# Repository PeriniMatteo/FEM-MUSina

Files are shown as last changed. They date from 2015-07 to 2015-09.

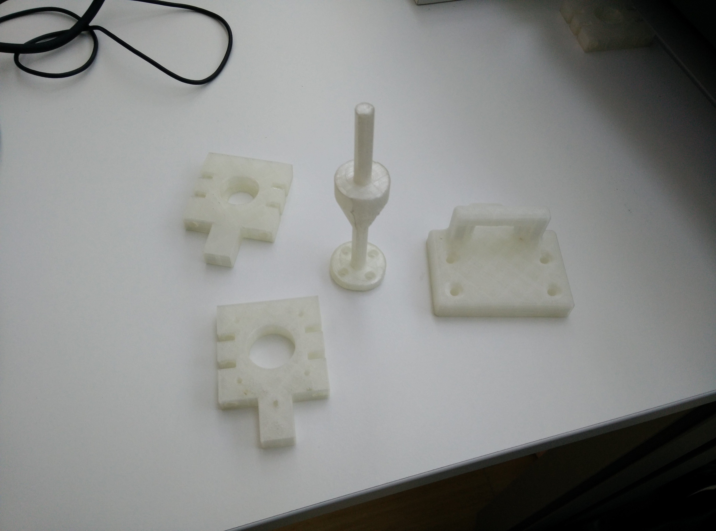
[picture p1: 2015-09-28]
pictures/3D-printed-components.jpg

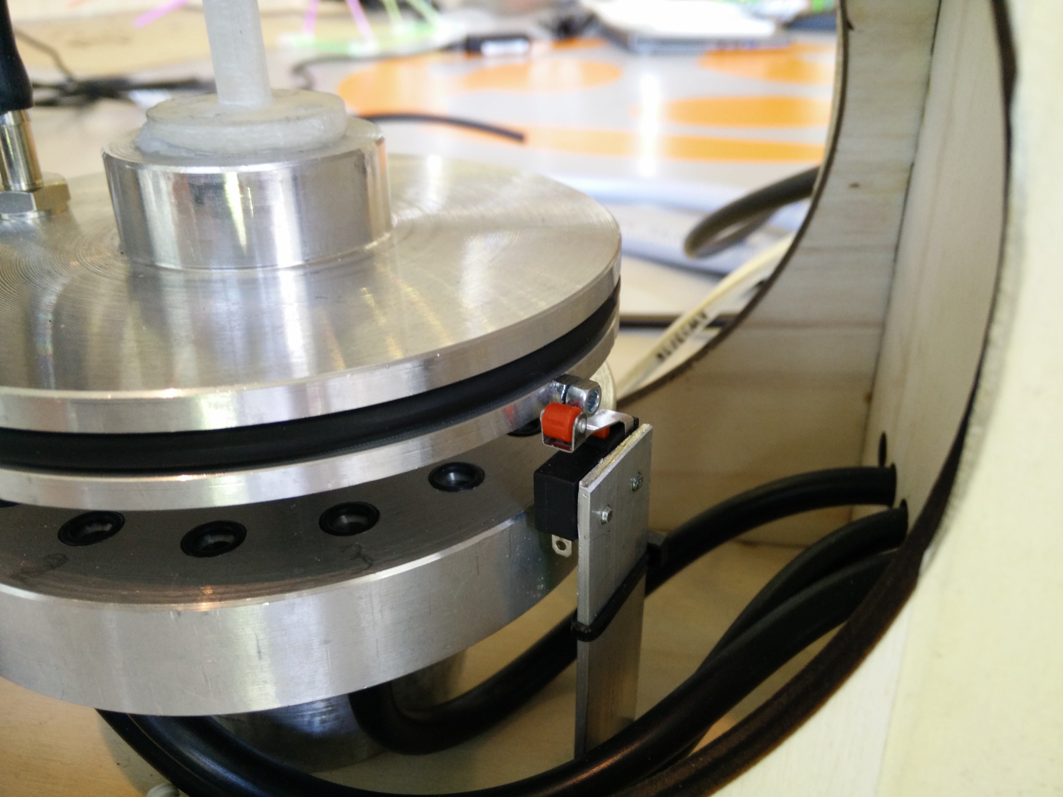
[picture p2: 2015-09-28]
pictures/end-stop-detail.jpg

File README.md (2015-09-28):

# FEM-MUSina
Repository che contiene informazioni sui componenti e strumentazione
necessari per costruire, programmare e gestire l'irrigatore FEM-MUSina.

L'intero progetto riportato è soggetto alla licenza GPL V3 (vedi file
[LICENSE](https://github.com/musefablab/FEM-MUSina/blob/master/LICENSE)).

G.Berti, D.Caset, S.Corradini, T.Dallapè, N.Oradini, M.Perini, G.Toller

FEM-MUSina: a seguito di un'idea partita all'interno della 
[Fondazione Edmund Mach](http://www.fmach.it), il 
[MUSE FabLab](http://fablab.muse.it), laboratorio di fabbricazione
digitale del Museo delle Scienze di Trento, ha contribuito a realizzare
un prototipo di macchina per l'irrigazione domestica di piante in vaso.
Questo progetto è nato con lo scopo di riuscire ad annaffiare svariate
piante solo quando queste ne hanno bisogno. Per fare questo ogni vaso è
dotato di un sensore dell’umidità del suolo e di una propria linea
irrigua. Il sistema, governato da un hardware e da un software creati a
partire dalla piattaforma informatica Arduino, dosa l’acqua in modo
adeguato alle esigenze di ogni pianta. Molti pezzi speciali del
prototipo, ad esclusione di quelli che richiedevano tornitura, sono
stati realizzati con gli strumenti in dotazione al FabLab: taglio laser,
stampante 3D, fresatrice. Nella progettazione si è puntato ad abbassare
i costi riducendo al massimo il numero di elettrovalvole/pompe. Nella
versione attuale, basata su un distributore rotante, una sola
elettrovalvola/pompa può alimentare sedici linee, ma è previsto di
espanderne il numero. Il controller scansiona periodicamente i sensori
di umidità nei vasi e, in base alla risposta, dosa la quantità d’acqua
somministrata a ciascuna pianta.

Gli elementi previsti per la costruzione completa della macchina
comprendono:

- [scheda Arduino](https://store.arduino.cc/product/A000066)
- [shield (autocostruito)](https://github.com/musefablab/FEM-MUSina/tree/master/schematics/pcb)
- [motor shield Arduino](https://www.arduino.cc/en/Main/ArduinoMotorShieldR3)
- componenti elettronici necessari per il circuito Arduino documentati
nella cartella [DATASHEET](https://github.com/musefablab/FEM-MUSina/tree/master/datasheet)
- switch di fine corsa
- servo
- motorino passo passo (Nema 17) 200 passi/giro
- elettrovalvola / pompa (12V)
- cablaggio per i sensori d'umidità
- tubi per flusso acqua
- alimentatore 12V collegato a presa di corrente

I dati e le tavole dei componenti sono reperibili nelle varie
cartelle:

- visualizzazione del modello solido della macchina dalle varie
prospettive - [IMAGES](https://github.com/musefablab/FEM-MUSina/tree/master/images)
- disegni tecnici dei componenti in compensato spesso 8mm da tagliare ed
assemblare ad incastro per il supporto esterno della macchina - 
[LASER](https://github.com/musefablab/FEM-MUSina/tree/master/laser)
- modelli 3D dei componenti di supporto fabbricati con stampa 3D - 
[STL](https://github.com/musefablab/FEM-MUSina/tree/master/stl)
- disegni tecnici delle parti meccaniche in alluminio e in gomma (parte
inferiore e superiore del disco forato, base di supporto al disco,
supporto rotazionale per giunto elastico, cuscinetto, cinghia, sezione
frontale della macchina) - [DRAWING](https://github.com/musefablab/FEM-MUSina/tree/master/drawings)
- schemi dei collegamenti elettronici, breadboard, PCB Arduino - 
[SCHEMATICS](https://github.com/musefablab/FEM-MUSina/tree/master/schematics)
- codice di programmazione dell'Arduino - [SRC](https://github.com/musefablab/FEM-MUSina/tree/master/src/FEM-MUSina)

Assemblare le parti meccaniche tornite e stampate inserendo il tutto nel
case dell'irrigatore completo dei supporti e dei componenti di fissaggio
come mostrato dalle immagini dei particolari nelle cartelle
[DRAWING](https://github.com/musefablab/FEM-MUSina/tree/master/drawings),
[IMAGES](https://github.com/musefablab/FEM-MUSina/tree/master/images),
e [PICTURES](https://github.com/musefablab/FEM-MUSina/tree/master/pictures).
Realizzare lo [shield](https://github.com/musefablab/FEM-MUSina/tree/master/schematics/pcb)
costituito dal [multiplexer](https://github.com/musefablab/FEM-MUSina/blob/master/datasheet/74HC4051.pdf)
ed i morsetti che controllano l'accensione dell'elettrovalvola/pompa, lo
[switch di fine corsa](https://github.com/musefablab/FEM-MUSina/blob/master/datasheet/micro-switch.pdf)
e i sensori di umidità. Per terminare lo shield effettuare gli opportuni
collegamenti e saldature (servo) tra dispositivi e pin preimpostati.
Una volta collegato il motorino passo passo al motor shield, unire lo
shield e il motor shield tra loro ed ai piedini della scheda Arduino
predisposti.
Per i vari cablaggi basarsi sugli schemi
[FEM-MUSina-schematic.pdf](https://github.com/musefablab/FEM-MUSina/blob/master/schematics/FEM-MUSina-schematic.pdf)
e [FEM-MUSina-breadboard.pdf](https://github.com/musefablab/FEM-MUSina/blob/master/schematics/FEM-MUSina-breadboard.pdf).
Collegare il controllore tramite cavo USB al computer con installato il
software [Arduino](https://www.arduino.cc/en/Main/Software). Dopo aver
scaricato il file [FEM-MUSina.ino](https://github.com/musefablab/FEM-MUSina/blob/master/src/FEM-MUSina/FEM-MUSina.ino)
aprirlo con Arduino IDE e caricare il codice. A questo punto il 
microcontrollore Arduino sarà programmato. È comunque possibile
personalizzare il codice in base delle proprie esigenze modificando una
serie di costanti all'interno della sezione iniziale "*objects and
variables declarations and definitions list*" sotto la voce "*user
customizable variables*" del software FEM-MUSina.ino: numero dei vasi da
irrigare, soglie del valore di umidità rilevate da Arduino in ogni vaso,
numero di passi del tipo di motore in utilizzo tra due fori, tempo di
innaffiamento, tempo d'attesa per lo svuotamento del tubicino di
irrigazione, tempo che intercorre tra la fine di un ciclo di irrigazione
ed il successivo.
In ultimo collegare i tubicini per il passaggio dell'acqua
dall'elettrovalvola/pompa al foro d'immissione nel revolver e i tubicini
diretti ai vasi ai fori che si vuole considerare per l'annaffiatura.

Enjoy watering!

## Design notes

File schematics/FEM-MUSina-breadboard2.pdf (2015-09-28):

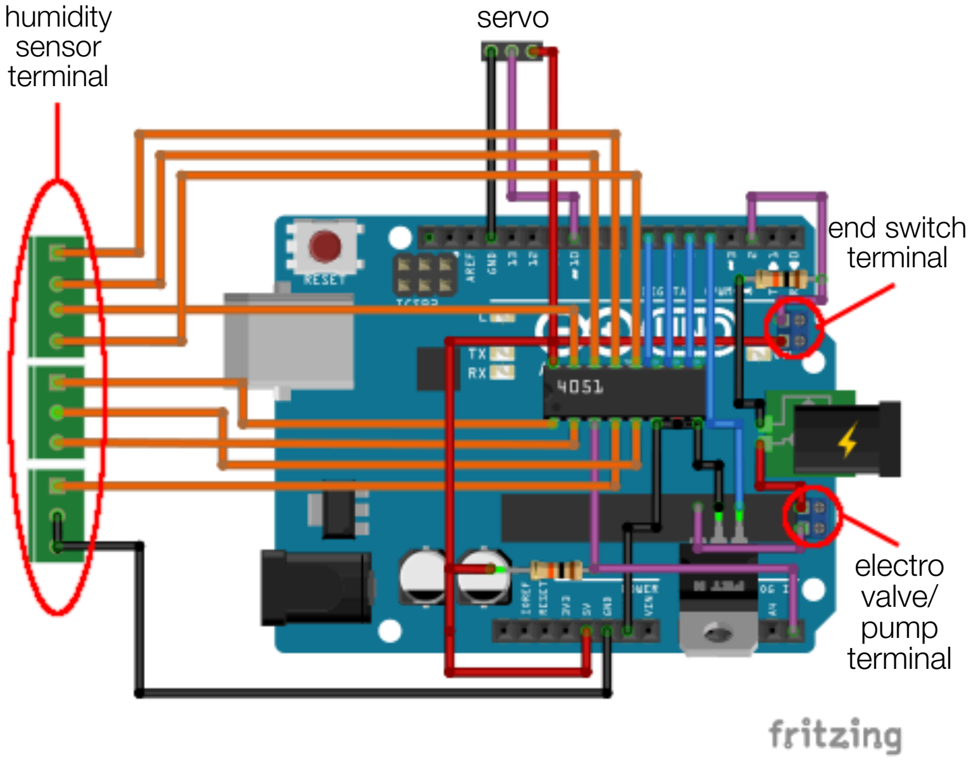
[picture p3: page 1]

humidity
sensor
terminal

end switch
terminal

electro
valve/
pump
terminal

servo

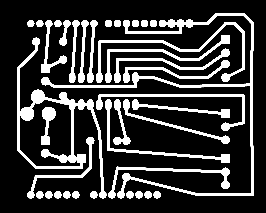
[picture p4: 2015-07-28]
schematics/pcb/to-mill/Shield-FEM-MUSina-path.png

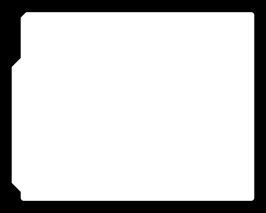
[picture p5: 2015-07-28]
schematics/pcb/to-mill/Shield-FEM-MUSina-cut.png

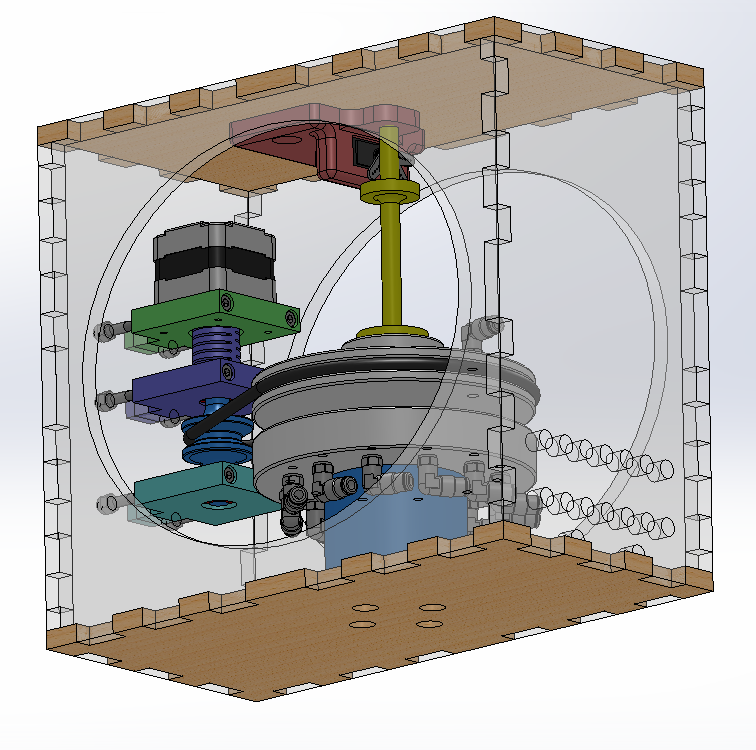
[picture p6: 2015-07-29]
images/FEM-MUSina-bottom-right-view.png

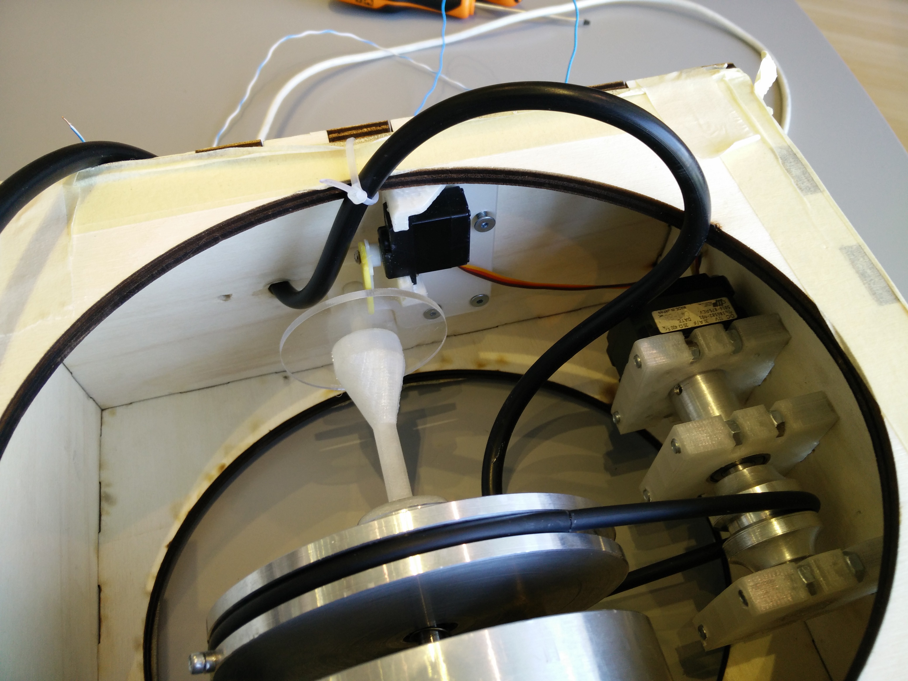
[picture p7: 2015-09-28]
pictures/FEM-MUSina-details3.jpg

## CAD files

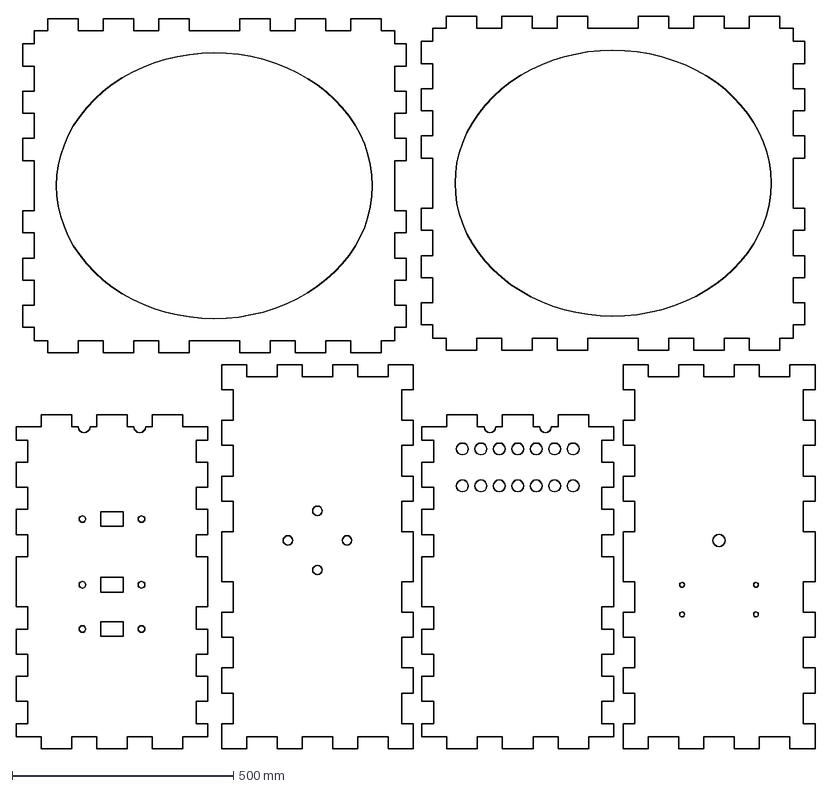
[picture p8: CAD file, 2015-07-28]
laser/FEM-MUSina-case.dxf
1804.0 x 1653.3 mm

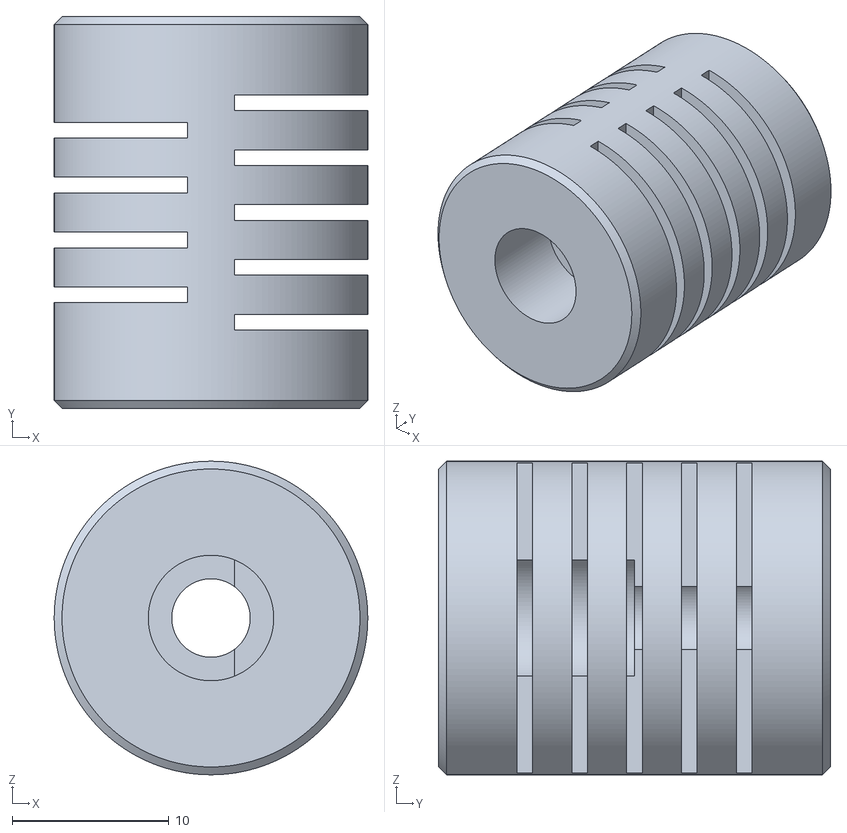
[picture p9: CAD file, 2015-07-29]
stl/FEM-MUSina-elastic-joint.stl
20.0 x 25.0 x 20.0

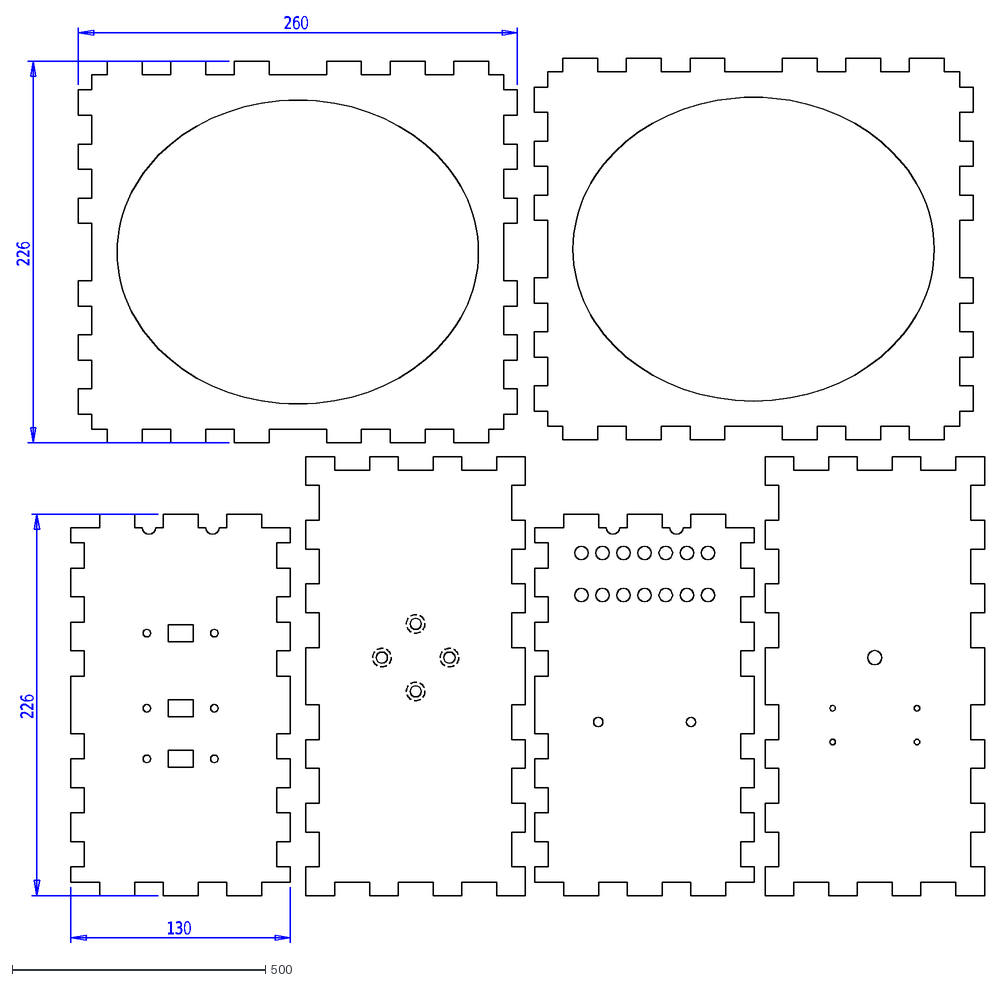
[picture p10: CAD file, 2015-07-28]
laser/FEM-MUSina-case-with-measure-not-for-laser.dxf
260
226
130

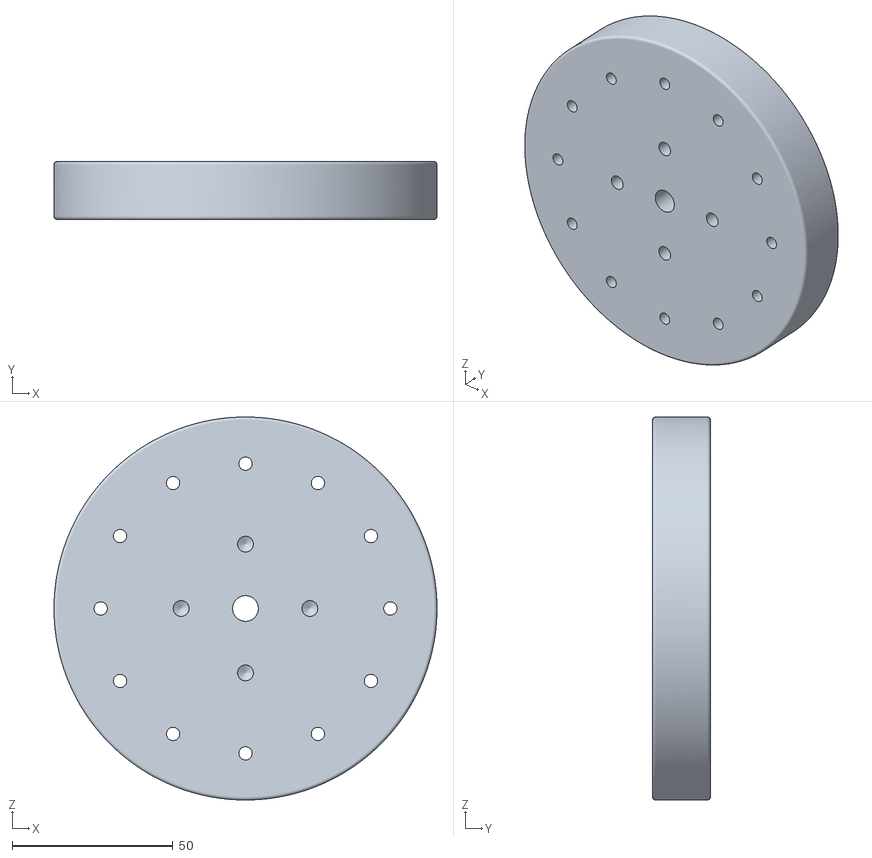
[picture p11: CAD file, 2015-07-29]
stl/FEM-MUSina-revolver-downside.stl
119.0 x 18.0 x 119.0

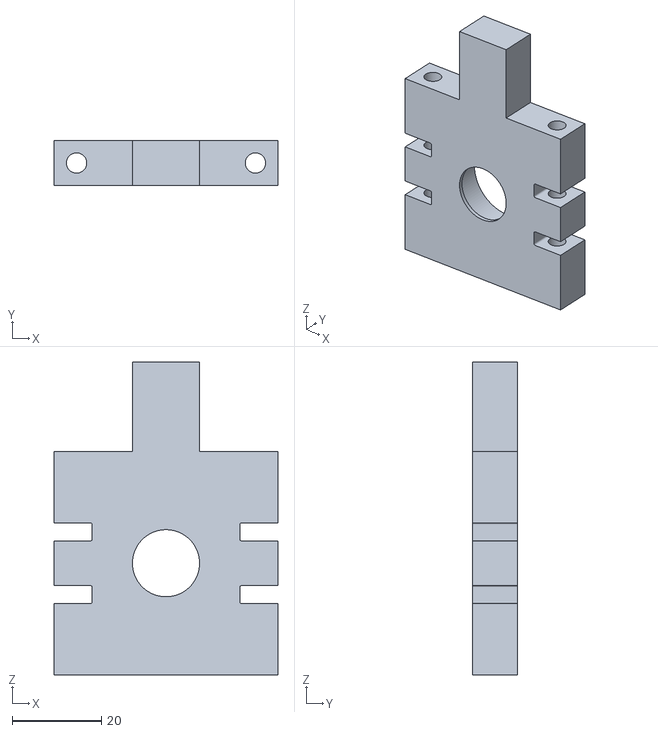
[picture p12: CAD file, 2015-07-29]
stl/FEM-MUSina-motor-support-up.stl
50.0 x 10.0 x 70.0

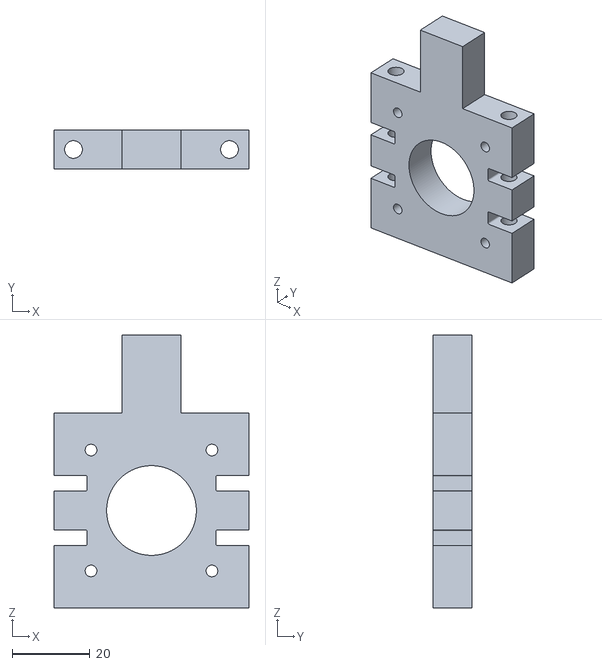
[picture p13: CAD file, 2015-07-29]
stl/FEM-MUSina-motor-support-middle.stl
50.0 x 10.00 x 70.0

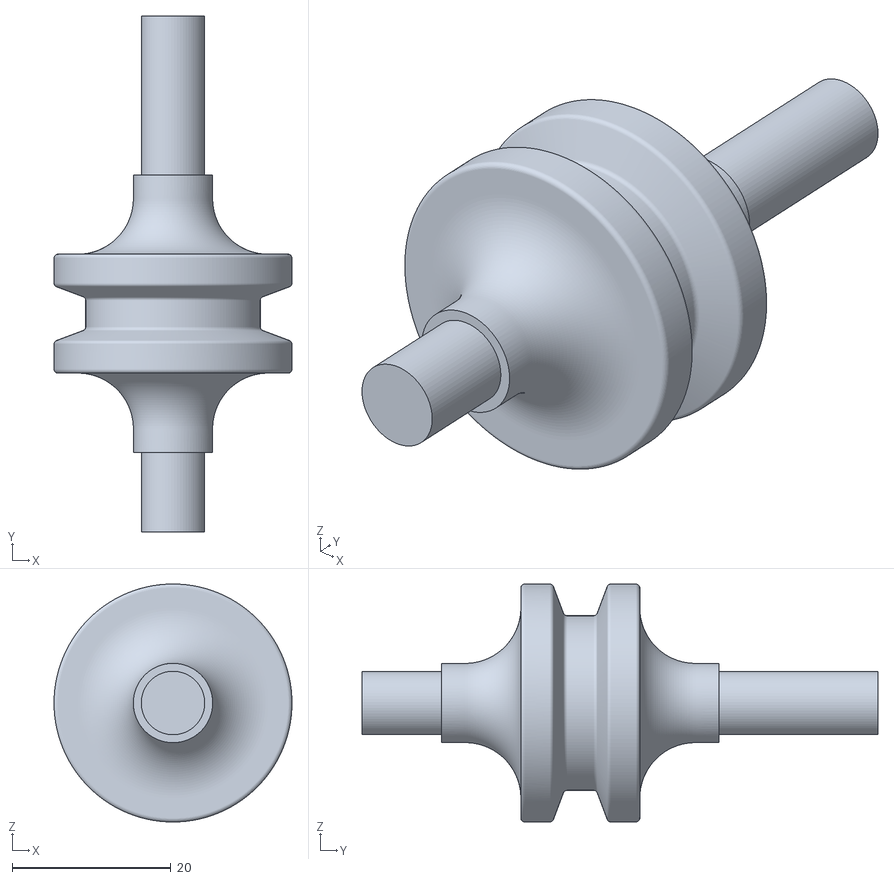
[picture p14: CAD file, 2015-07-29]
stl/FEM-MUSina-pulley.stl
30.0 x 65.0 x 30.0

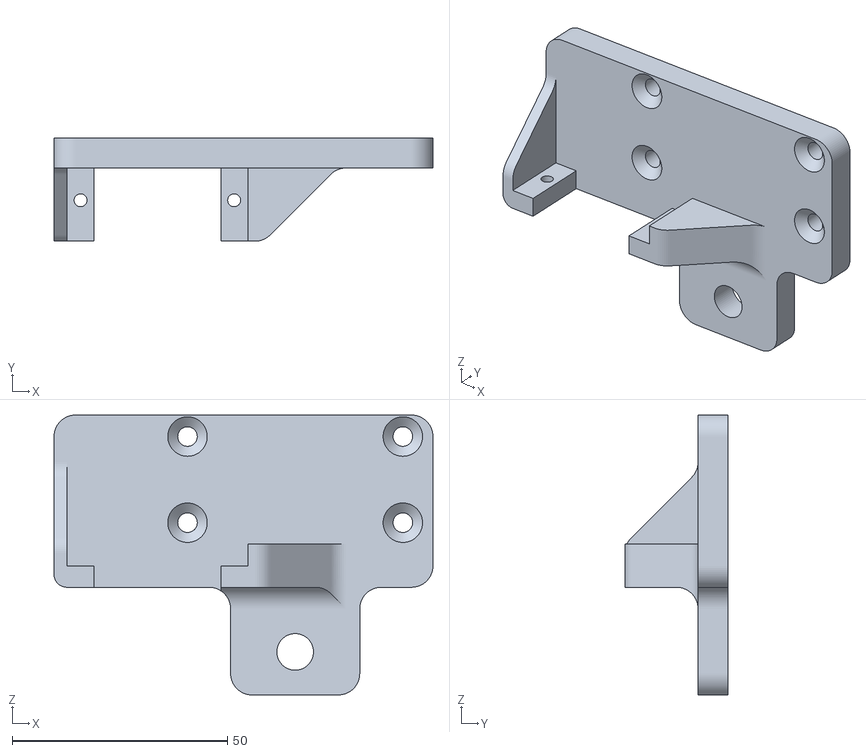
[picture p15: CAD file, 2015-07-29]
stl/FEM-MUSina-servo-holder.stl
88.0 x 24.0 x 65.0

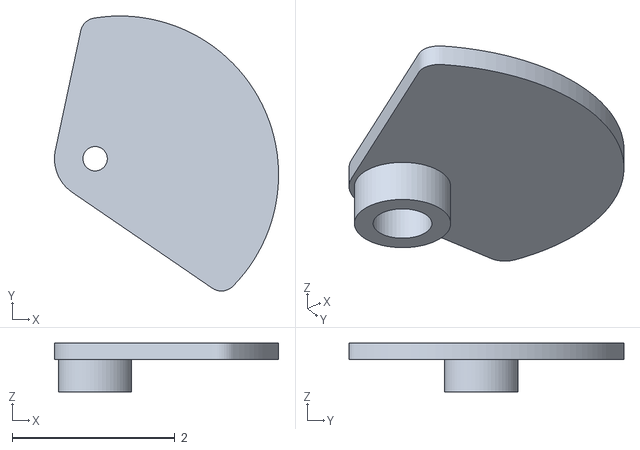
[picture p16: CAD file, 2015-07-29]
stl/FEM-MUSina-servo-cam.stl
2.75 x 3.38 x 0.6

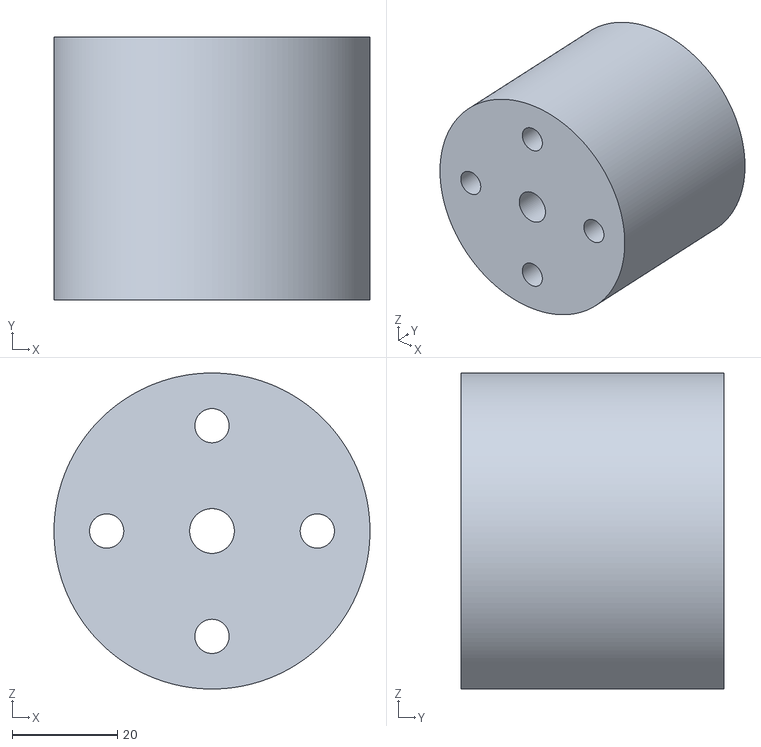
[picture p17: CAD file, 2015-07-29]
stl/FEM-MUSina-base.stl
60.0 x 50.0 x 60.0

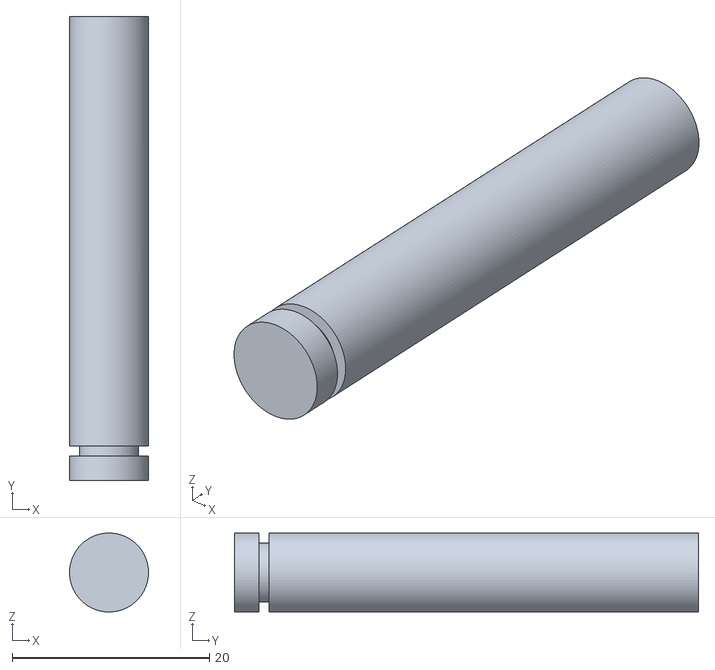
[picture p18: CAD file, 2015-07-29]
stl/FEM-MUSina-central-pin.stl
8.00 x 47.0 x 8.00

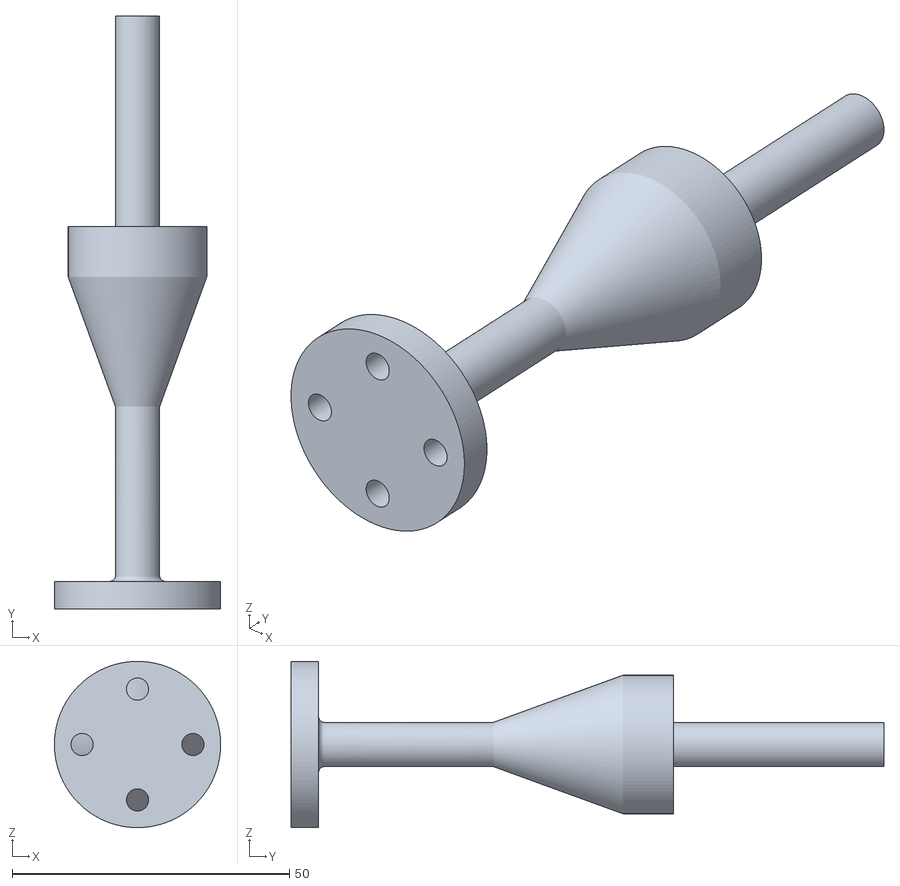
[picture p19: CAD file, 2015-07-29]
stl/FEM-MUSina-press-down-lever.stl
30.0 x 107.0 x 30.0

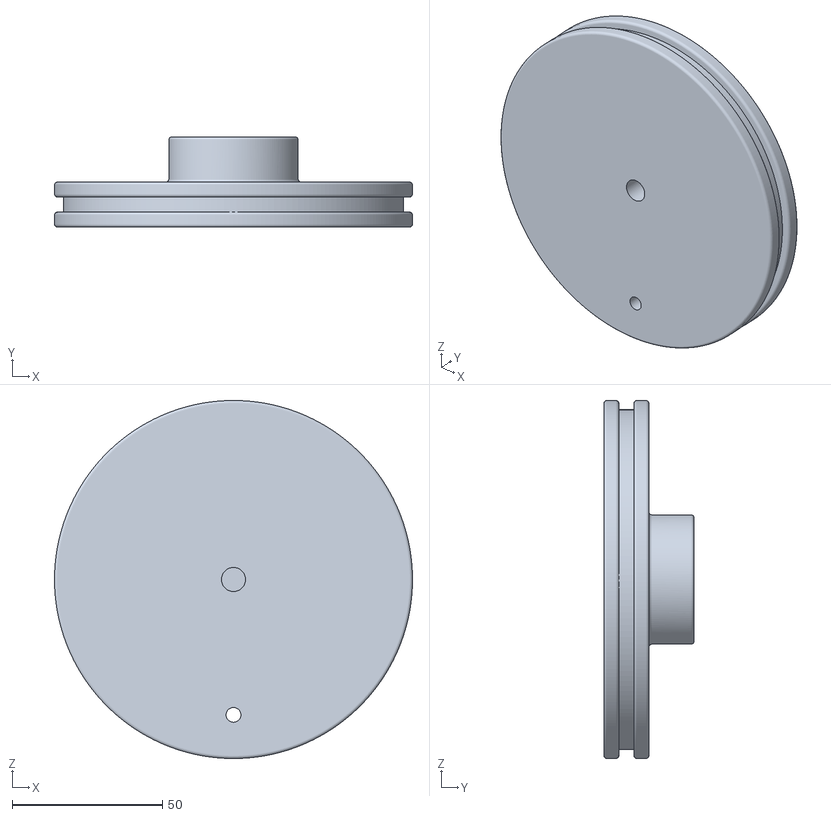
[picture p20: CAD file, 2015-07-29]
stl/FEM-MUSina-revolver-upside.stl
119.0 x 30.0 x 119.0

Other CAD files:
stl/FEM-MUSina-motor-support-down.stl

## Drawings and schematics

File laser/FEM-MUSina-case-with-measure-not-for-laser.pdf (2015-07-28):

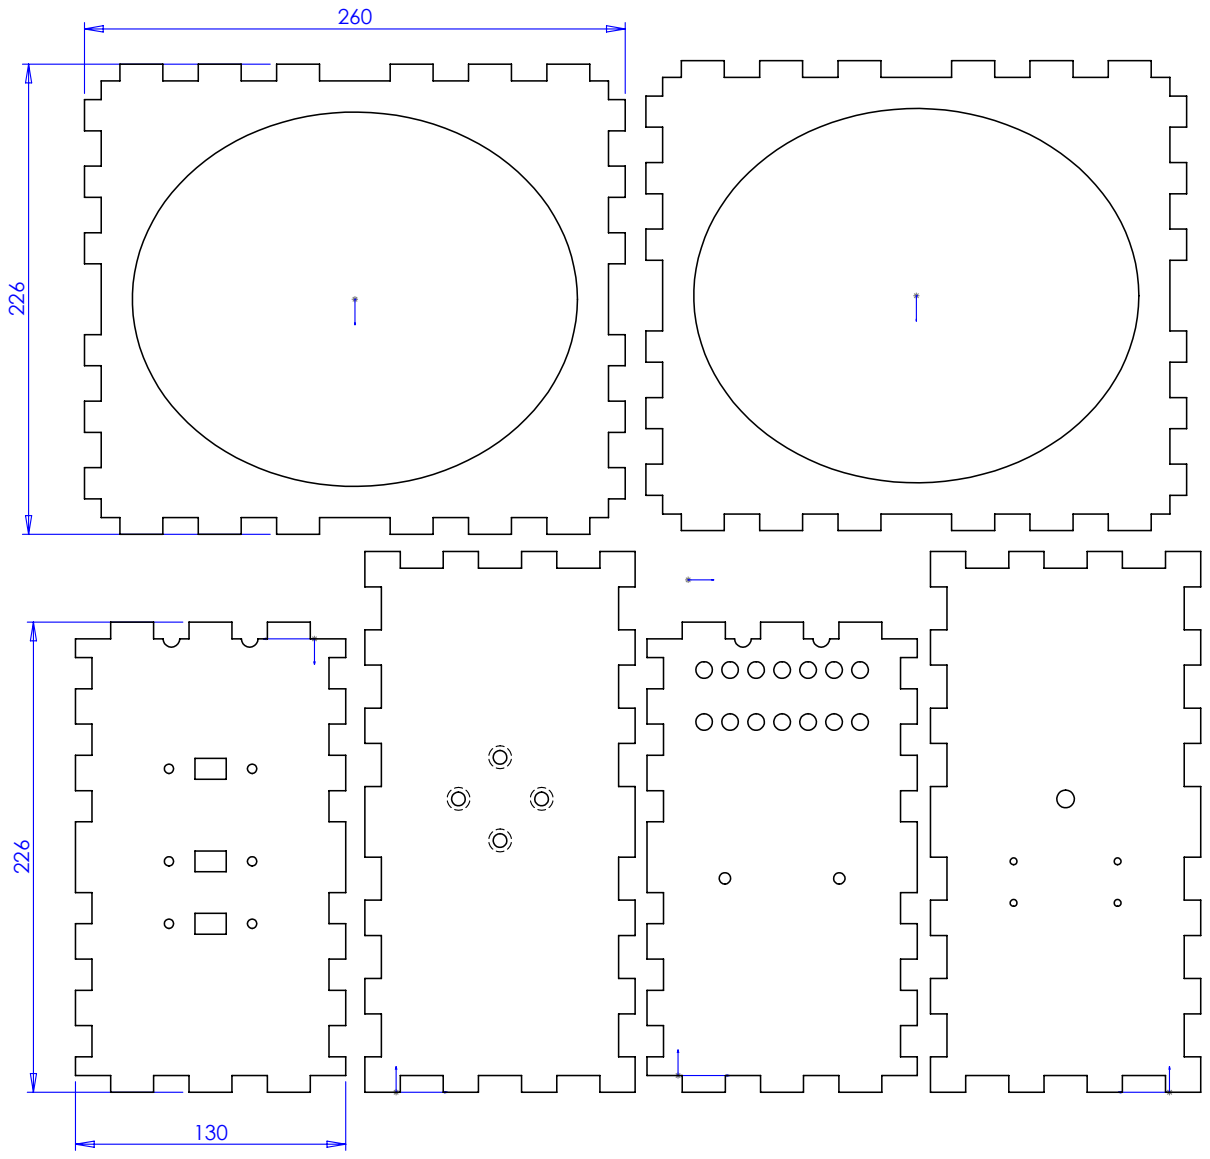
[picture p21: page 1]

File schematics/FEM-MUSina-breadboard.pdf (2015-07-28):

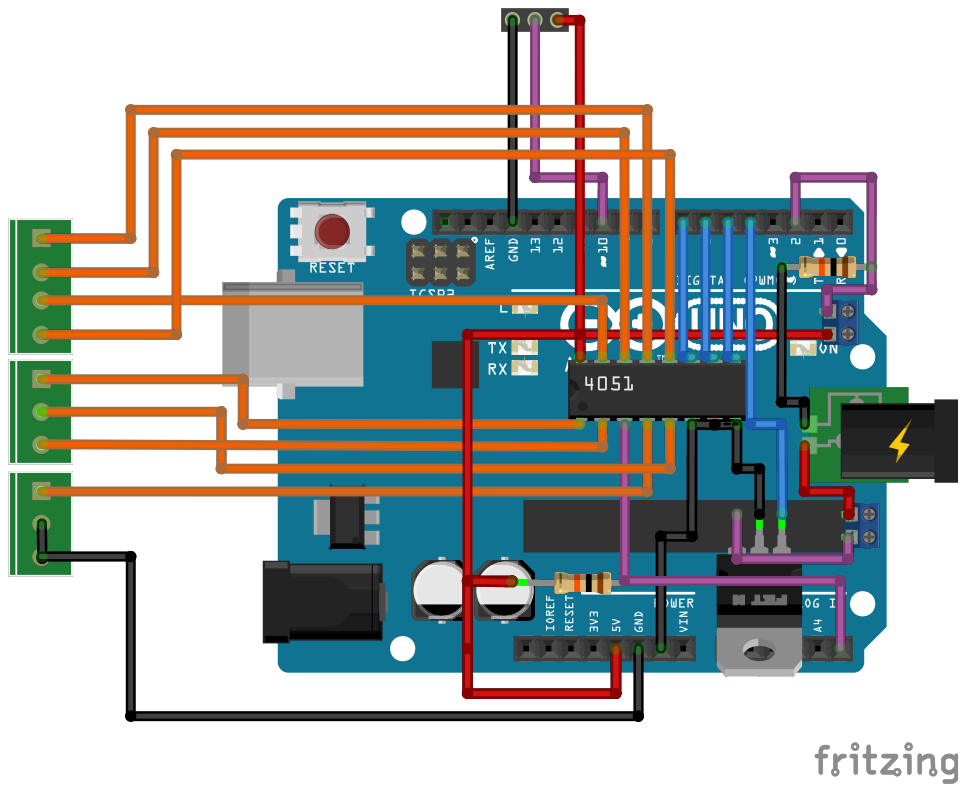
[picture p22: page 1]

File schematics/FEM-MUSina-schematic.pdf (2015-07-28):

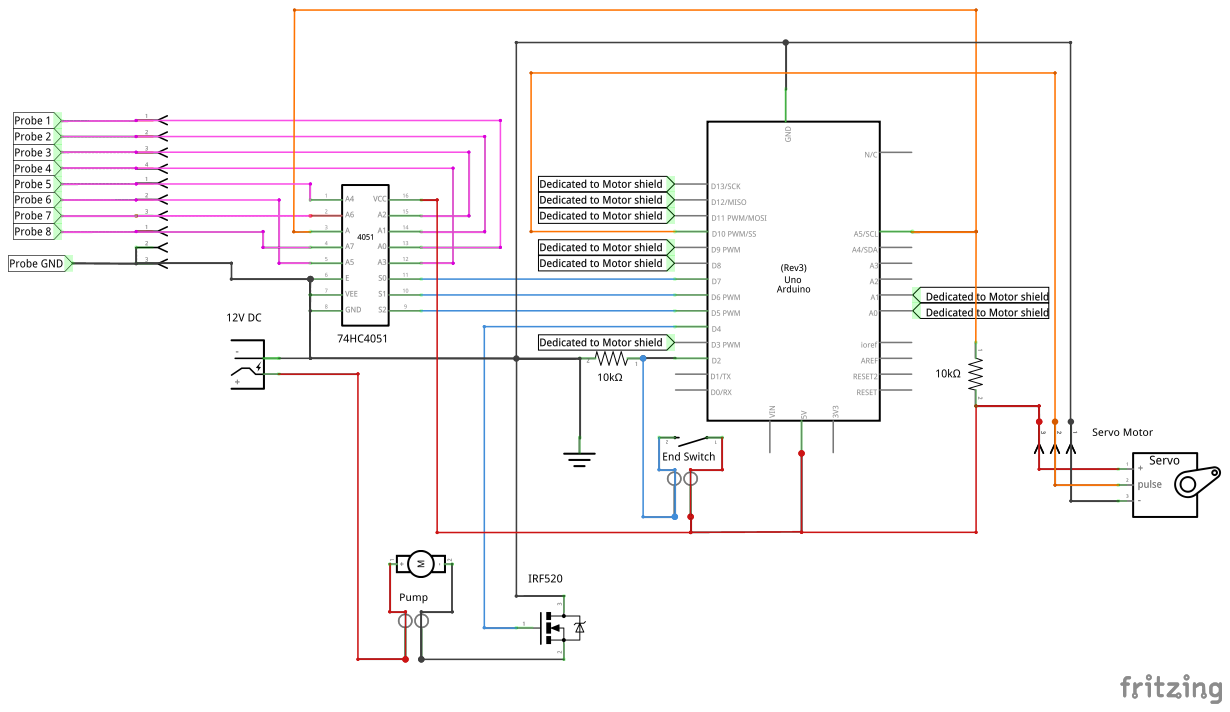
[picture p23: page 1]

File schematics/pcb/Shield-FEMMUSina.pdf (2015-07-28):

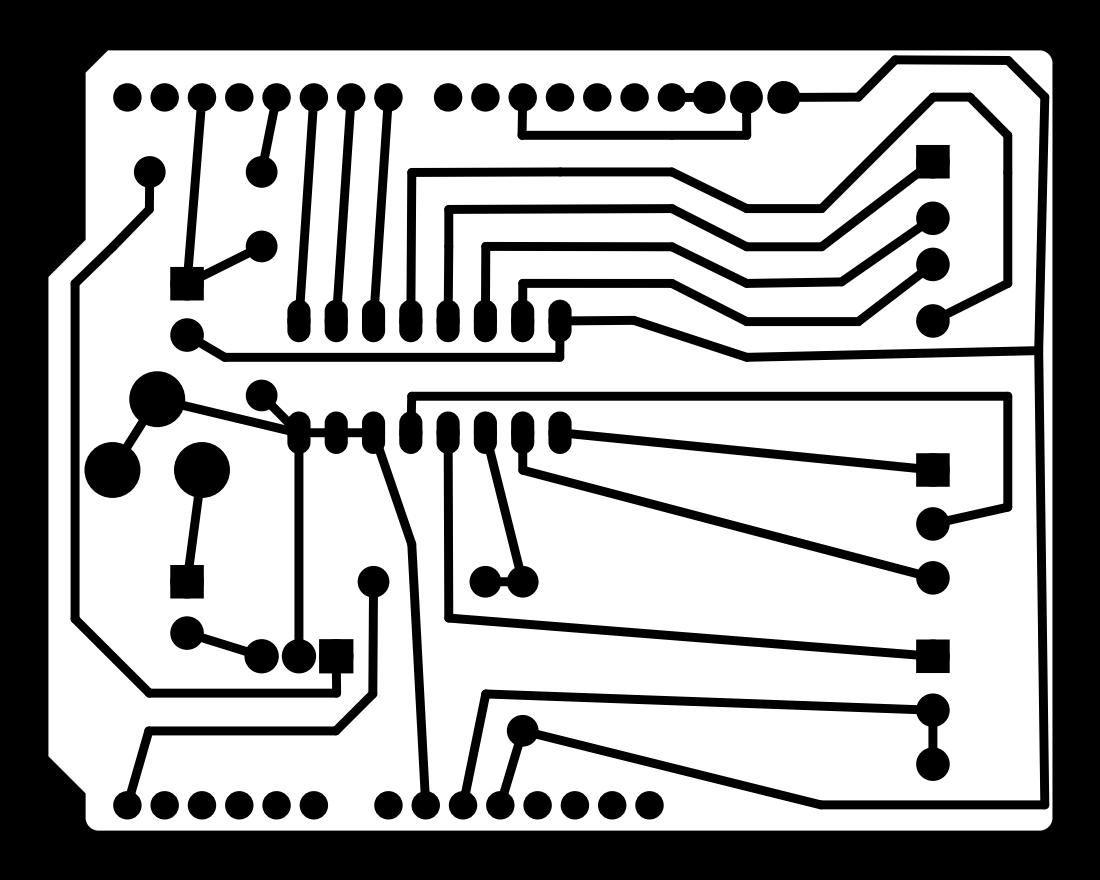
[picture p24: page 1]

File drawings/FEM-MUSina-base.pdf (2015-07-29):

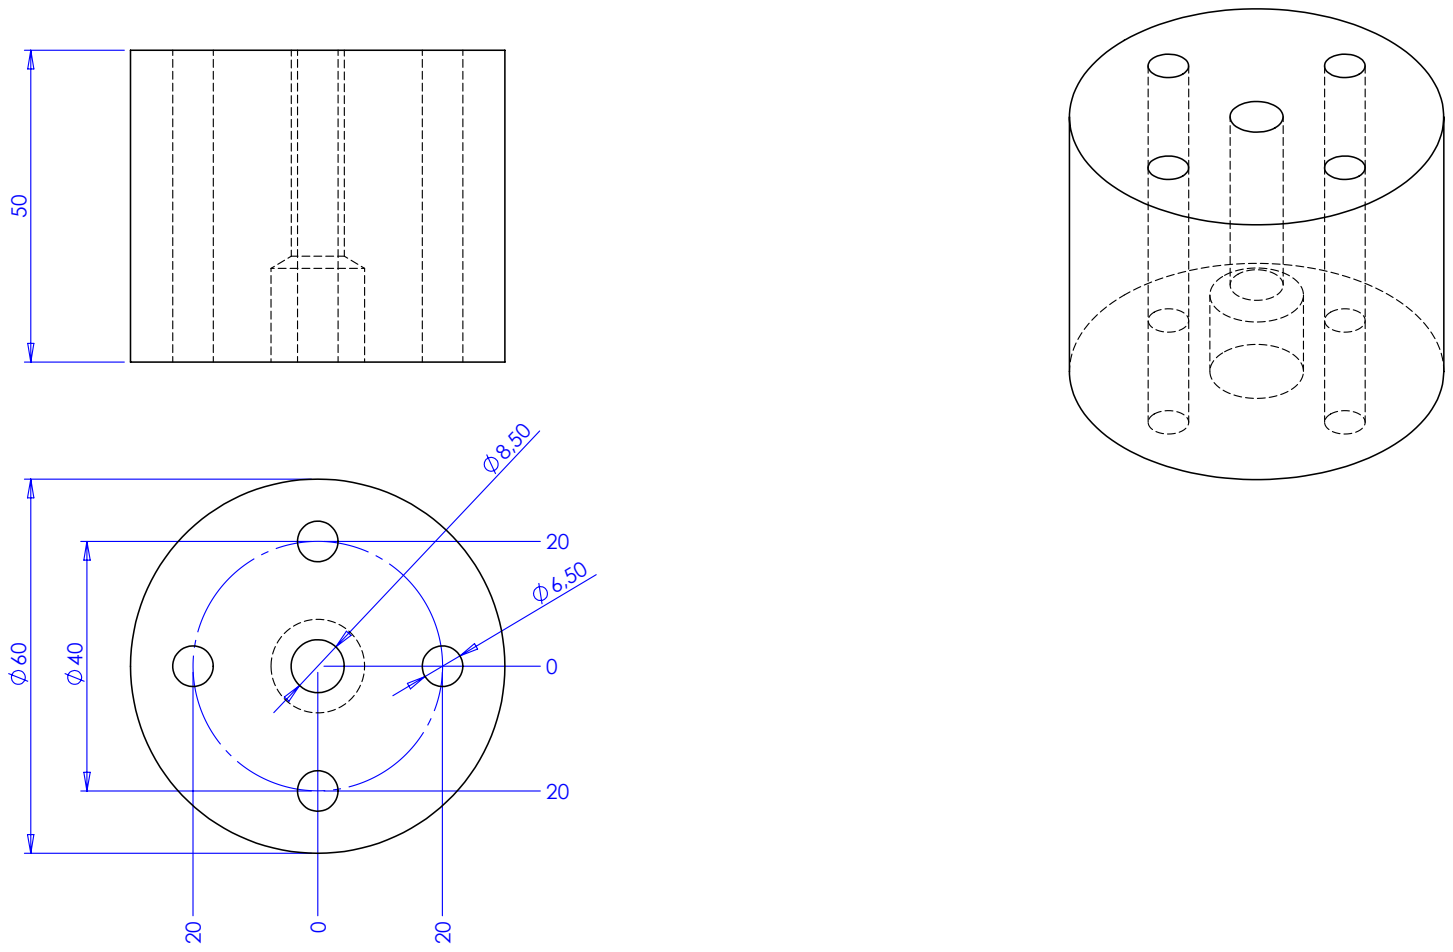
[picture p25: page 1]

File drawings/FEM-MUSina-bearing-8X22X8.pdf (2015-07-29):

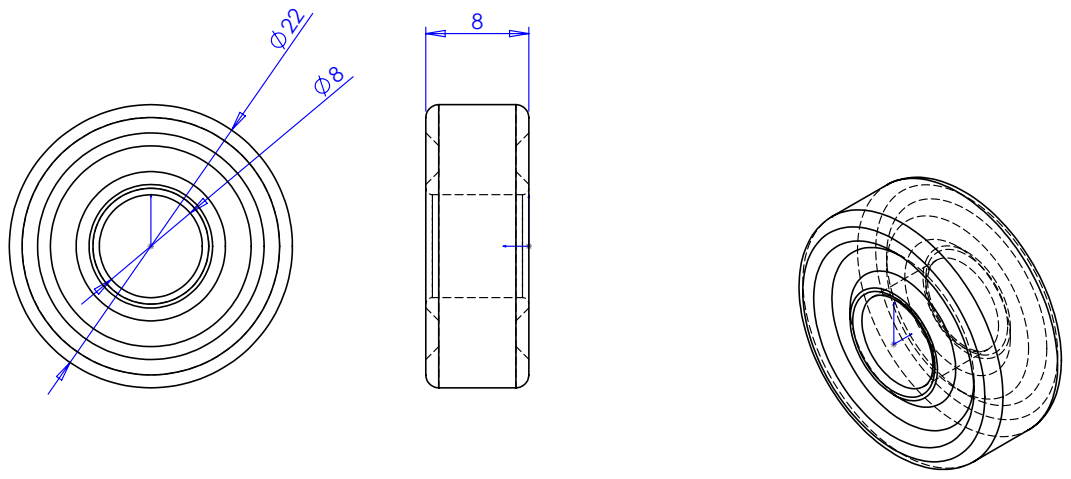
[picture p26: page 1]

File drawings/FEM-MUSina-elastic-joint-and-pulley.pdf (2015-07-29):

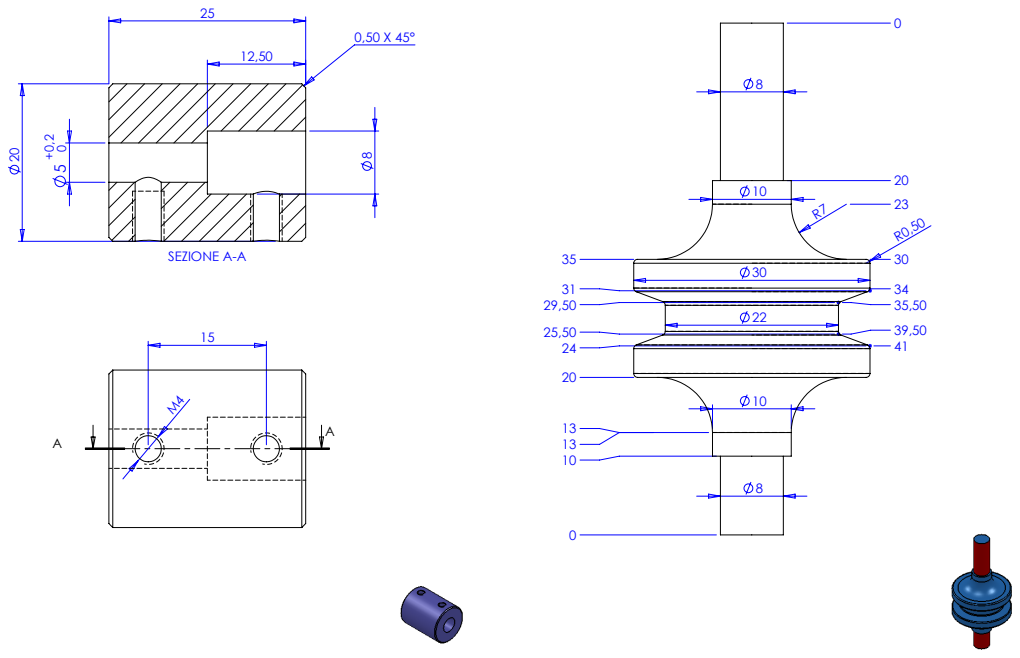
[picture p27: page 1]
SEZIONE A-A

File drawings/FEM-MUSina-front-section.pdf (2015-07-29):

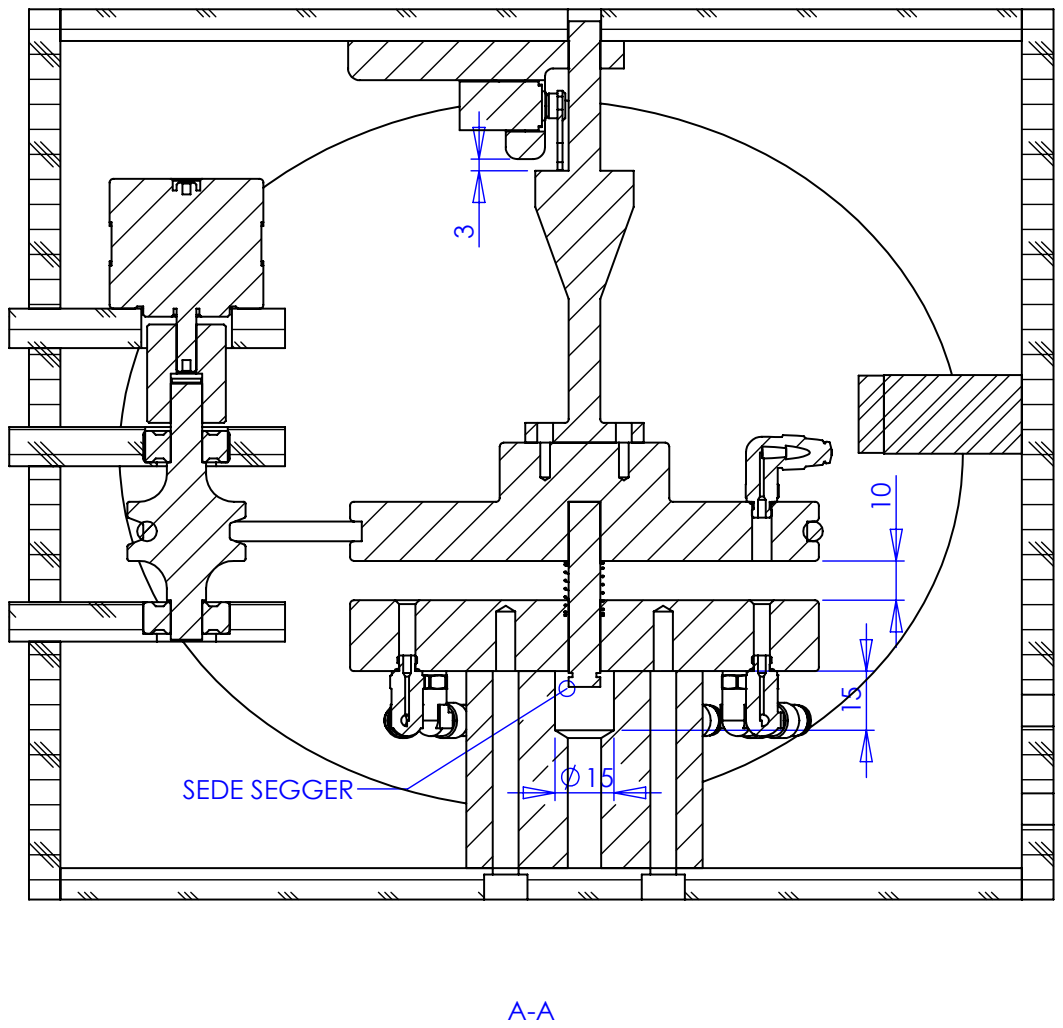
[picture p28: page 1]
SEDE SEGGER

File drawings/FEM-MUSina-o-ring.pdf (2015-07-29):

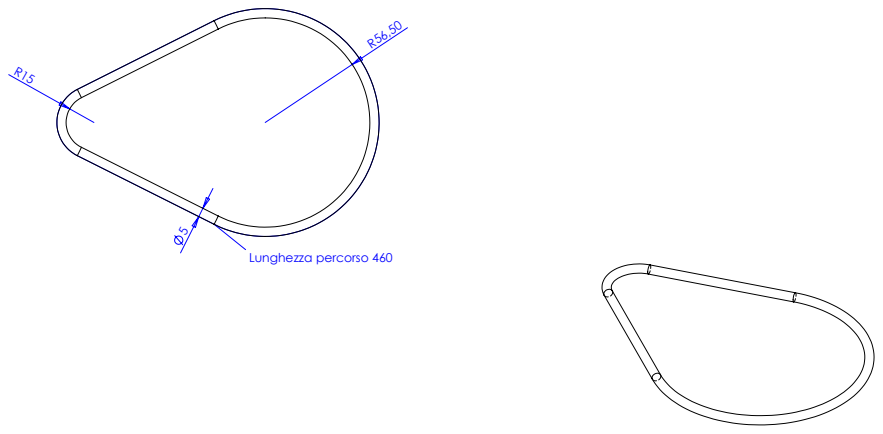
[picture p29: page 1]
Lunghezza percorso 460

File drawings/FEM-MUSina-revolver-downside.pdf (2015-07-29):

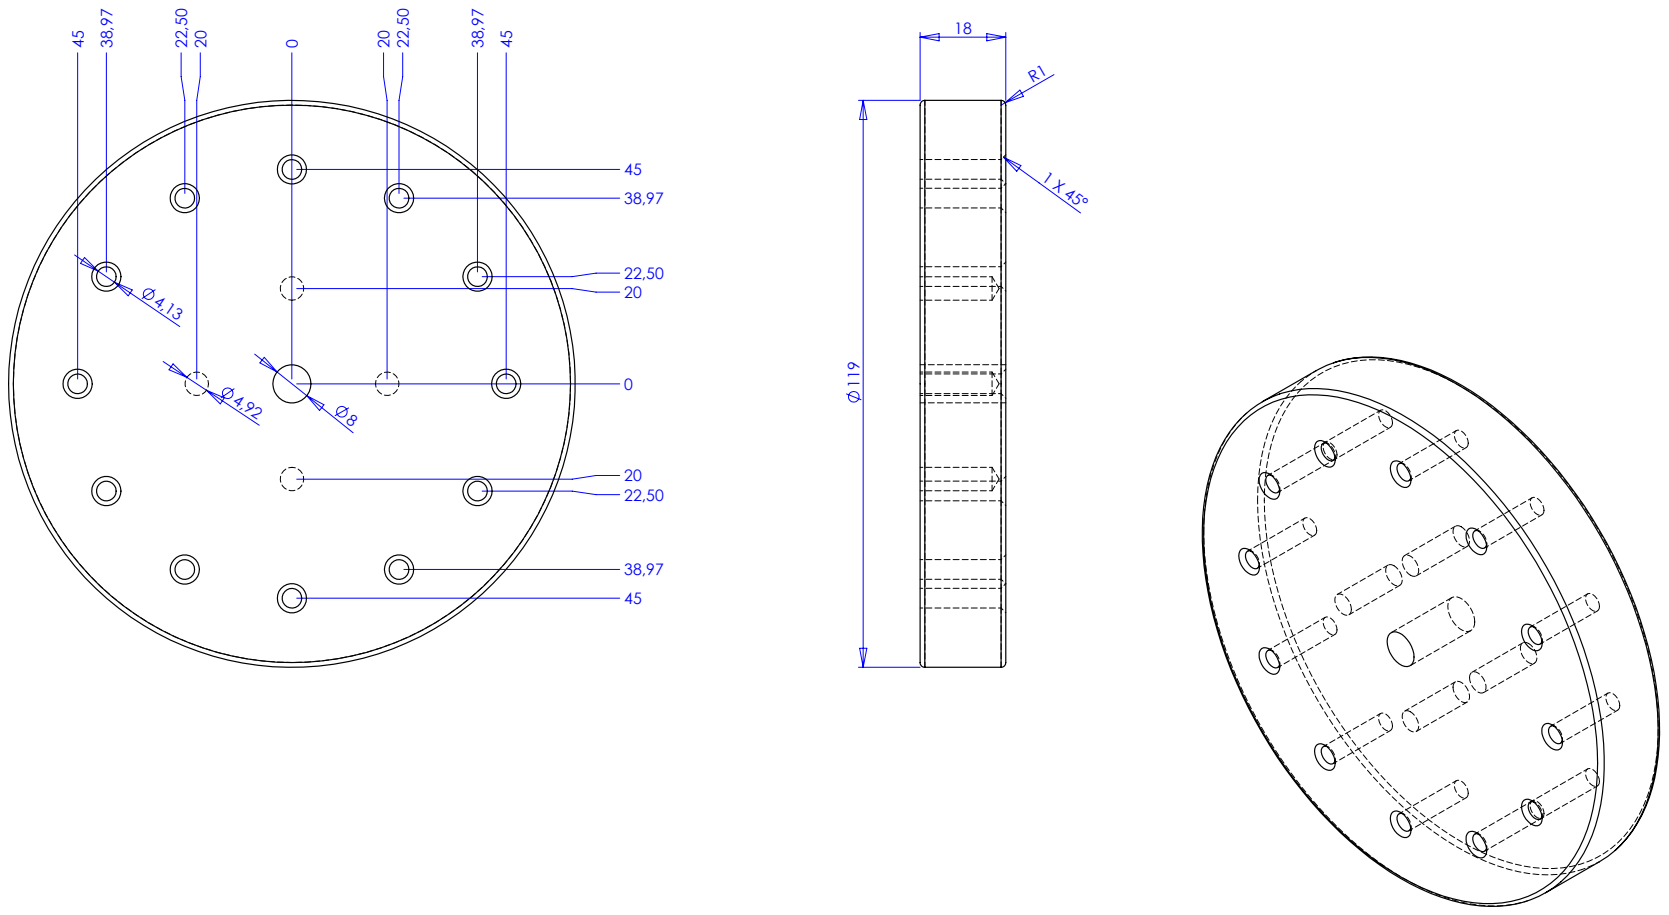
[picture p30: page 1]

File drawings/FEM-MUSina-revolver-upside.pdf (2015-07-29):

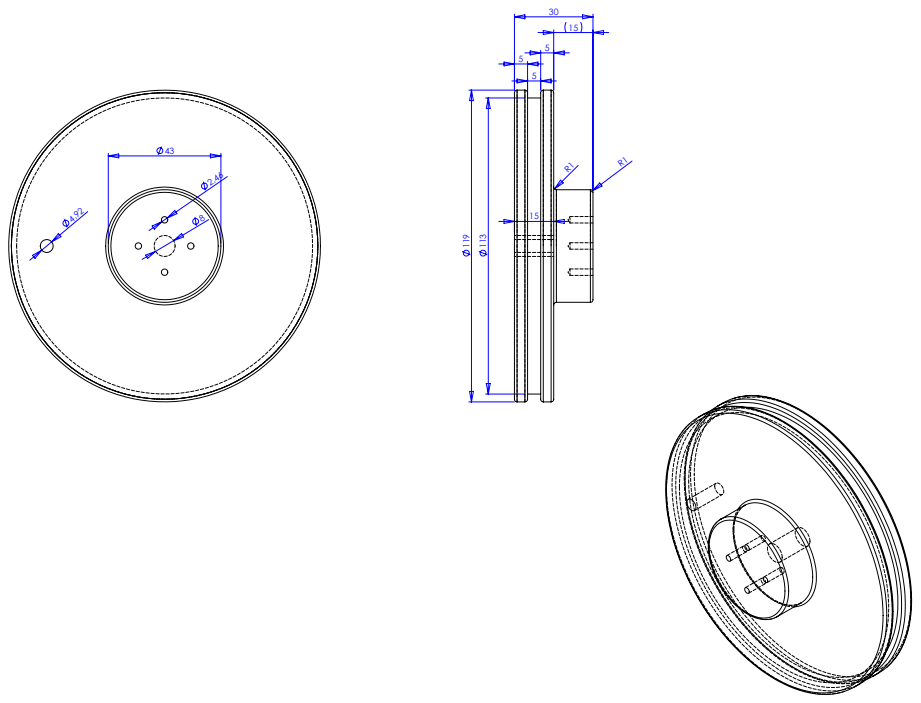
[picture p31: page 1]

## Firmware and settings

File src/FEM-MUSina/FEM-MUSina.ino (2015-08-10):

/*
#                     FEM-MUSina IRRIGATOR
#
# Software to manage FEM-MUSina irrigator
#
# Copyright (c) 2015 Tiziana Dallapè
# Copyright (c) 2015 Matteo Perini
# Copyright (c) 2015 Giambattista Toller
#
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
# See LICENSE file for details
#
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
# See https://github.com/musefablab/FEM-MUSina for detailed project
*/



#include <Servo.h>   //add libraries


/*----------------------------------------------------------------------
 objects and variables declarations and definitions list
----------------------------------------------------------------------*/
  Servo myservo;          //create a Servo object
  int ServoPin = 10;      //attach servo to pin 10
  int motorPinDirA = 12;  //attach motor to pins 12 13 3 11
  int motorPinDirB = 13;
  int motorPinPwmA = 3;
  int motorPinPwmB = 11;
  int EVPin = 4;          //attach electro valve to pin 4
  int stopPin = 2;        //attach switch to pin 2
//service variables
  int index = 0;          //vase index 
  int dir = 1;            //default motor direction
  int nStep = 0;          //definition of motor steps
  long int T0;            //variable to store Arduino's timer value [ms]
//variables for the selection of input pin at the 4051 multiplexer
  int r0 = 0;     //bit value of the selected input pin at the 4051 (s0)
  int r1 = 0;     //bit value of the selected input pin at the 4051 (s1)
  int r2 = 0;     //bit value of the selected input pin at the 4051 (s2)
//declaration and initialization of array of motor step
  boolean PwmA[8] = {1,1,1,0,1,1,1,0};
  boolean PwmB[8] = {1,0,1,1,1,0,1,1};
  boolean DirA[8] = {1,1,1,1,0,0,0,0};
  boolean DirB[8] = {1,1,0,0,0,0,1,1};
//user customizable variables
  const int n_pots = 8;     /*change value of index according to number
                              of pots you have; default: 8 pots*/
  int resistance[n_pots] = {0,0,0,0,0,0,0,0};/*declaration and
                                               initialization at 1023
                                               points of array, where
                                               resistance values
                                               (humidity proxy) will be
                                               checked*/
  int threshold[n_pots] = {900,900,900,900,900,900,900,900};/*declara-
                                                              tion and
                                                              initiali-
                                                              zation of
                                                              array of
                                                              water
                                                              threshold
                                                              of every
                                                              pot*/
  int steps = 195;          /*number of motor steps between two pipes;
                              default: 195 steps for our motor*/
  int water_time = 25000;   //valve opening time [ms]
  int emptying_delay = 2000;/*water complete emptying time through
                              pipes; default: 2000ms*/
  int check_delay = 180000; /*time between the end of one watering cycle
                              and the next one*/



void setup() {
/*----------------------------------------------------------------------
 SETUP FUNCTION
   this function runs once at the start of the program which is used to
   define initial environmental settings
----------------------------------------------------------------------*/
  pinMode(motorPinDirA, OUTPUT);  //motor "A" channel direction
  pinMode(motorPinDirB, OUTPUT);  //motor "B" channel direction
  pinMode(motorPinPwmA, OUTPUT);  //motor "A" impulse
  pinMode(motorPinPwmB, OUTPUT);  //motor "A" impulse
  pinMode(7, OUTPUT);             //s0 multiplexer byte index
  pinMode(6, OUTPUT);             //s1 multiplexer byte index
  pinMode(5, OUTPUT);             //s2 multiplexer byte index
  pinMode(EVPin, OUTPUT);         //electro valve control
  pinMode(A5, INPUT);             //ground resistance reading
  pinMode(stopPin, INPUT);        //switch reading
  Serial.begin(9600);             //serial initialization
  T0 = millis();                  //set T0 to millis()
  myservo.attach(ServoPin);       //initialize Servo motor
  myservo.write(0);               //set Servo position to 0deg
}


void step(int dir) {
/*----------------------------------------------------------------------
 motor moving function
----------------------------------------------------------------------*/
  if(dir == 1) {                                //move forward
    nStep = (nStep+1)%8;
    digitalWrite(motorPinDirA, DirA[nStep]);
    digitalWrite(motorPinDirB, DirB[nStep]);
    digitalWrite(motorPinPwmA, PwmA[nStep]);
    digitalWrite(motorPinPwmB, PwmB[nStep]);
  }else {                                       //backward
    nStep = (nStep+1)%8;
    digitalWrite(motorPinDirA, DirA[7-nStep]);     
    digitalWrite(motorPinDirB, DirB[7-nStep]);
    digitalWrite(motorPinPwmA, PwmA[7-nStep]);
    digitalWrite(motorPinPwmB, PwmB[7-nStep]);
  }
}


void check_ground_resistance() {
/*----------------------------------------------------------------------
 resistance check function
   the ground has variable resistance in function of its humidity.
   Resistance is measured by voltage divider, which is red by AD
   converter at pin A5. Resistance is checked on every pots
----------------------------------------------------------------------*/
  Serial.println("Checking...");
  for(index = 0; index <= (n_pots-1); index++) {   
    r0 = bitRead(index, 0);     //read a number as bits (first digit)
    r1 = bitRead(index, 1);     //read a number as bits (second digit)
    r2 = bitRead(index, 2);     //read a number as bits (third digit)
    digitalWrite(7, r0);        //set multiplexer to read indexth input
    digitalWrite(6, r1);
    digitalWrite(5, r2);
    int multiplexerOutput = analogRead(A5);/*read the multiplexer output
                                             value*/
    resistance[index] = multiplexerOutput; /*set data in resistance
                                             array*/
  }
}


void water(int to_be_watered) {
/*----------------------------------------------------------------------
 watering function
   this function recieves the index (0...n_pots) of the pot to be
   watered, basing on resistance check (humidity proxy); revolver moves
   forward to the right position, reached it, Servo pulls down the
   revolver which joints its gap with the lower part of machine, the
   valve is opened and the water flows through the pipe watering the pot
   for the water_time time; the valve is closed, wait for emptying_delay
   time for water complete emptying, then Servo pulls up the revolver
----------------------------------------------------------------------*/
  Serial.println("Going to the right position...");
  for(index = (to_be_watered * steps * 2); index >= 0; index--) {
    Serial.println("Step");
    step(1);
    delay(2);         //change this value to change speed; default: 2
  }
  Serial.println("Position reached!");
  myservo.write(70);                 //set servo to 70deg
  Serial.println("Pull down...");
  delay(500);
  digitalWrite(EVPin, HIGH);
  delay(water_time);
  Serial.println("Watering...");
  Serial.println("Please wait...");
  digitalWrite(EVPin, LOW);
  Serial.println("Turn off the valve...");
  delay(emptying_delay);
  Serial.println("Please wait a little...");
  myservo.write(0);                  //set servo to starting position
  Serial.println("Pull up...");
}


void stepper_reset() {
/*----------------------------------------------------------------------
 motor backward move function
   function moves backward the motor as long as revolver reach the
   switch to set the home position
----------------------------------------------------------------------*/
  analogWrite(motorPinPwmA, 255);
  analogWrite(motorPinPwmB, 255);
  Serial.println("I'm going...");
  while(!(digitalRead(stopPin) == HIGH)) {
    step(-1);
    delay(2);         //change this value to change speed; default: 2
  }
  Serial.println("Home reached!");
  delay(2000);
}


void loop() {
/*----------------------------------------------------------------------
 LOOP FUNCTION
   watering loop routine runs countless times calling some functions;
   when spended time since last watering is higher than check_delay
   time, watering loop starts checking resistance: if the ground is dry
   (low humidity) tension is high and the ground resistance is high too,
   so if the checked resistance in one pot is higher than threshold,
   that plant will be watered
----------------------------------------------------------------------*/
  analogWrite(motorPinPwmA, 0);
  analogWrite(motorPinPwmB, 0);
  if((millis() - T0) > check_delay) {
    T0 = millis();
    Serial.println("Check resistance...");   
    check_ground_resistance();
    for(index = 0; index <= (n_pots-2); index++) {
      Serial.print(resistance[index]);
      Serial.print(" , ");
    }
    Serial.println(resistance[(n_pots-1)]);
    Serial.println("");
    Serial.println("Controlling values...");
    for(index = 0; index <= (n_pots-1); index++) {  
      if(resistance[index] > threshold[index]) {
        Serial.print("Resistance at the ");
        Serial.print(index+1);
        Serial.println("th vase voltage is too high!");
        Serial.println("Try to water the plant");
        stepper_reset();
        Serial.println("Go to home position...");
        int to_be_watered = index+1;
        water(to_be_watered);
        Serial.println("Water the plant");
        Serial.println("Plant watered!");
        break;
      }else {
        Serial.print("Plant ");
        Serial.print(index+1);
        Serial.println(" doesn't need water...");
      }
     Serial.println("Waiting for new resistance check...");
     Serial.println("");
    }
  }
}

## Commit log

2015-07-28 Uploaded Fritzing project of the shield
    [FEM-MUSina-fritzing-project.fzz]
2015-07-28 Added breadboard and electric circuits
2015-07-28 Uploaded png files for pcb milling
2015-07-28 Added drawings of the case ready for the laser cutter
    [FEM-MUSina-case.dxf]
2015-07-28 Added drawings with quote and correct dxf file
    [FEM-MUSina-case-with-measure-not-for-laser.dxf, FEM-MUSina-case.dxf]
2015-07-29 Uploaded some 3D models
    [FEM-MUSina-base.stl, FEM-MUSina-central-pin.stl, FEM-MUSina-elastic-joint.stl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]
2015-08-10 Added Arduino sketch

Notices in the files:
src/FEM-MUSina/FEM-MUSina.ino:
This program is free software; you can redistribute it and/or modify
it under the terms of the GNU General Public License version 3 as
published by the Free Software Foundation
